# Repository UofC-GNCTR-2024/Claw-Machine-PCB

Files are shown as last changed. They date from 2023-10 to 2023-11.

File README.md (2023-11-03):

# Claw-Machine-PCB
PCB for the UofC GNCTR 2024 claw machine

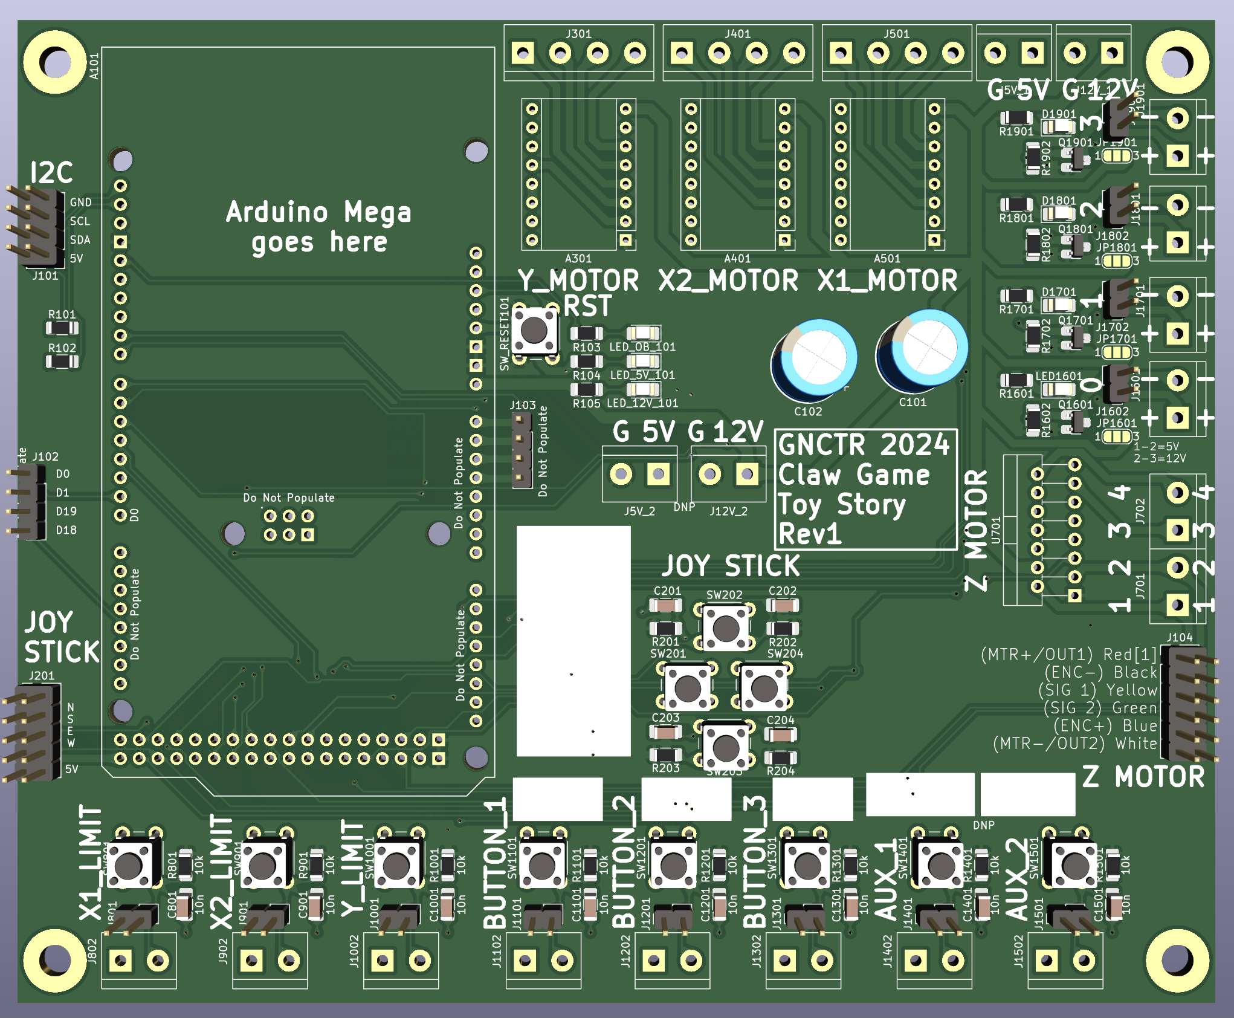
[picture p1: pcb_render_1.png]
PCB Render 1


## Main Components
1. 3x Stepper Motor Drivers
    * 2x will drive Y-axis, and 1x will drive X-axis
    * Model: A4988 Breakout
        * [Guide 1 - lastminuteengineers.com](https://lastminuteengineers.com/a4988-stepper-motor-driver-arduino-tutorial/)
    * The [microstep mode](https://lastminuteengineers.com/a4988-stepper-motor-driver-arduino-tutorial/#:~:text=power%20supply%20pins.-,Microstep%20Selection%20Pins,-The%20A4988%20driver) is locked in 1/16th Step Mode.
    * Add LEDs to each control signal
    * Signals (MCU to Driver, for each driver): STEP, DIR, EN

2. 1x DC Motor Driver
    * 1x for the claw to drop
    * Model: L298N (package: multiwatt vertical)
        * [Datasheet 1](https://www.sparkfun.com/datasheets/Robotics/L298_H_Bridge.pdf)
    * L298N contains 2x H-Bridges, so it can drive the 2x motors
    * Add LEDs to each control signal

3. Countdown Clock I2C Connector
    * Uses I2C (so only one bus)
    * Connection over 2.54mm headers

4. 10x Buttons and Limit Switches
    * 3x Limit Switches, 3x User Buttons, 2x Spare
    * Use 5.08mm screw terminal in parallel with 2.54mm header
    * Make them active-low, with external pull-up resistors
    * Put them in parallel with 6mm through-hole push buttons for validation

5. Control Stick
    * Model: [4-Way Switched Discrete Joystick](https://www.amazon.ca/Joystick-Classic-Competition-Arcade1up-Replacement/dp/B0BWWW8Z2J/ref=sr_1_15)
    * Basically 4x more buttons
    * Label them NESW, and use a common GND (5-pin 2.54mm header, but two of them side-by-side)

6. 1x Microcontroller System
    * Model: Arduino Mega 2560 clone
    * Footprint available via plugin

7. 4x General Power Output Channels
    * Use AO3420 MOSFETs, to be able to drive LEDs in the frame, etc.
    * Add a 3-way solder jumper to select between 5V or 12V power
    * Can be used fo LED strip lighting. One channel will be for the 12V claw solenoid.

8. Voltage Input Rails
    * 5V and 12V rails
    * Inputs via 5.08mm screw terminals
    * Powered from computer PSU

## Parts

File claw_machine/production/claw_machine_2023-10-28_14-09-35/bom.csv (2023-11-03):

Designator | Footprint | Quantity | Value | LCSC Part #
A101 | Arduino_Mega2560_R3_Shield | 1 | Arduino_Mega2560_R3_Shield
A301, A401, A501 | Pololu_Breakout-16_15.2x20.3mm | 3 | Pololu_Breakout_A4988
C1001, C1101, C1201, C1301, C1401, C1501, C201, C202, C203, C204, C801, C901 | 1206 | 12 | 10n
C101, C102 | CP_Radial_D10.0mm_P5.00mm_P7.50mm | 2 | 100u
D1701, D1801, D1901, LED1601, LED_12V_101, LED_5V_101, LED_OB_101 | 1206 | 7 | LED
H101, H102, H103, H104 | MountingHole_4.3mm_M4_Pad_TopBottom | 4 | MountingHole
J1001, J1101, J1201, J1301, J1401, J1501, J1602, J1702, J1802, J1902, J801, J901 | PinHeader_1x02_P2.54mm_Vertical | 12 | Conn_01x02
J1002, J1102, J1202, J12V_1, J1302, J1402, J1502, J1601, J1701, J1801, J1901, J5V_1, J701, J702, J802, J902 | TerminalBlock_bornier-2_P5.08mm | 16 | Screw_Terminal_01x02
J101 | PinHeader_2x04_P2.54mm_Vertical | 1 | ~
J102, J103 | PinHeader_1x04_P2.54mm_Vertical | 2 | Conn_01x04
J104 | PinHeader_2x06_P2.54mm_Vertical | 1 | Conn_02x06_Odd_Even
J201 | PinHeader_2x05_P2.54mm_Vertical | 1 | Conn_02x05_Odd_Even
J301, J401, J501 | TerminalBlock_bornier-4_P5.08mm | 3 | Screw_Terminal_01x04
JP1601, JP1701, JP1801, JP1901 | SolderJumper-3_P1.3mm_Open_RoundedPad1.0x1.5mm_NumberLabels | 4 | SolderJumper_3_Open
Q1601, Q1701, Q1801, Q1901 | SOT-23-MassivePads-HandSolder | 4 | AO3400A
R1001, R105, R1101, R1201, R1301, R1401, R1501, R1602, R1702, R1802, R1902, R201, R202, R203, R204, R801, R901 | 1206 | 17 | 10k
R101, R102 | 1206 | 2 | 3k3
R103, R104, R1601, R1701, R1801, R1901 | 1206 | 6 | 2k2
SW1001, SW1101, SW1201, SW1301, SW1401, SW1501, SW201, SW202, SW203, SW204, SW801, SW901, SW_RESET101 | SW_PUSH_6mm | 13 | SW_Push
U701 | TO-220-15_P2.54x2.54mm_StaggerOdd_Lead4.58mm_Vertical | 1 | L298N

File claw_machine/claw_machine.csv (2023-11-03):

Source: | /home/user/GitHub/Claw-Machine-PCB/claw_machine/claw_machine.kicad_sch
Date: | Fri 03 Nov 2023 04:45:17 PM
Tool: | Eeschema 7.0.8
Generator: | /app/share/kicad/plugins/bom_csv_grouped_by_value.py
Component Count: | 114
Collated Components:
Item | Qty | Reference(s) | Value | LibPart | Footprint | Datasheet | DNP
1 | 1 | A101 | Arduino_Mega2560_R3_Shield | PCM_arduino-library:Arduino_Mega2560_R3_Shield | PCM_arduino-library:Arduino_Mega2560_R3_Shield | https://docs.arduino.cc/hardware/mega-2560
2 | 3 | A301, A401, A501 | Pololu_Breakout_A4988 | Driver_Motor:Pololu_Breakout_A4988 | Module:Pololu_Breakout-16_15.2x20.3mm | https://www.pololu.com/product/2980/pictures
3 | 2 | C101, C102 | 100u | Device:C_Polarized | Capacitor_THT:CP_Radial_D10.0mm_P5.00mm_P7.50mm | ~
4 | 12 | C201, C202, C203, C204, C801, C901, C1001, C1101, C1201, C1301, C1401, C1501 | 10n | Device:C | Capacitor_SMD:C_1206_3216Metric_Pad1.33x1.80mm_HandSolder | ~
5 | 7 | D1701, D1801, D1901, LED1601, LED_5V_101, LED_12V_101, LED_OB_101 | LED | Device:LED | LED_SMD:LED_1206_3216Metric_Pad1.42x1.75mm_HandSolder | ~
6 | 4 | H101, H102, H103, H104 | MountingHole | Mechanical:MountingHole_Pad | MountingHole:MountingHole_4.3mm_M4_Pad_TopBottom | ~
7 | 16 | J5V_1, J12V_1, J701, J702, J802, J902, J1002, J1102, J1202, J1302, J1402, J1502, J1601, J1701, J1801, J1901 | Screw_Terminal_01x02 | Connector:Screw_Terminal_01x02 | TerminalBlock:TerminalBlock_bornier-2_P5.08mm | ~
8 | 2 | J5V_2, J12V_2 | Screw_Terminal_01x02 | Connector:Screw_Terminal_01x02 | TerminalBlock:TerminalBlock_bornier-2_P5.08mm | ~ | DNP
9 | 1 | J101 | ~ | Connector_Generic:Conn_02x04_Odd_Even | Connector_PinHeader_2.54mm:PinHeader_2x04_P2.54mm_Vertical | ~
10 | 2 | J102, J103 | Conn_01x04 | Connector_Generic:Conn_01x04 | Connector_PinHeader_2.54mm:PinHeader_1x04_P2.54mm_Vertical | ~
11 | 1 | J104 | Conn_02x06_Odd_Even | Connector_Generic:Conn_02x06_Odd_Even | Connector_PinHeader_2.54mm:PinHeader_2x06_P2.54mm_Vertical | ~
12 | 1 | J201 | Conn_02x05_Odd_Even | Connector_Generic:Conn_02x05_Odd_Even | Connector_PinHeader_2.54mm:PinHeader_2x05_P2.54mm_Vertical | ~
13 | 3 | J301, J401, J501 | Screw_Terminal_01x04 | Connector:Screw_Terminal_01x04 | TerminalBlock:TerminalBlock_bornier-4_P5.08mm | ~
14 | 12 | J801, J901, J1001, J1101, J1201, J1301, J1401, J1501, J1602, J1702, J1802, J1902 | Conn_01x02 | Connector_Generic:Conn_01x02 | Connector_PinHeader_2.54mm:PinHeader_1x02_P2.54mm_Vertical | ~
15 | 4 | JP1601, JP1701, JP1801, JP1901 | SolderJumper_3_Open | Jumper:SolderJumper_3_Open | Jumper:SolderJumper-3_P1.3mm_Open_RoundedPad1.0x1.5mm_NumberLabels | ~
16 | 4 | Q1601, Q1701, Q1801, Q1901 | AO3400A | Transistor_FET:AO3400A | Library:SOT-23-MassivePads-HandSolder | http://www.aosmd.com/pdfs/datasheet/AO3400A.pdf
17 | 2 | R101, R102 | 3k3 | Device:R | Resistor_SMD:R_1206_3216Metric_Pad1.30x1.75mm_HandSolder | ~
18 | 6 | R103, R104, R1601, R1701, R1801, R1901 | 2k2 | Device:R | Resistor_SMD:R_1206_3216Metric_Pad1.30x1.75mm_HandSolder | ~
19 | 17 | R105, R201, R202, R203, R204, R801, R901, R1001, R1101, R1201, R1301, R1401, R1501, R1602, R1702, R1802, R1902 | 10k | Device:R | Resistor_SMD:R_1206_3216Metric_Pad1.30x1.75mm_HandSolder | ~
20 | 13 | SW201, SW202, SW203, SW204, SW801, SW901, SW1001, SW1101, SW1201, SW1301, SW1401, SW1501, SW_RESET101 | SW_Push | Switch:SW_Push | Button_Switch_THT:SW_PUSH_6mm | ~
21 | 1 | U701 | L298N | Driver_Motor:L298N | Package_TO_SOT_THT:TO-220-15_P2.54x2.54mm_StaggerOdd_Lead4.58mm_Vertical | http://www.st.com/st-web-ui/static/active/en/resource/technical/document/datasheet/CD00000240.pdf

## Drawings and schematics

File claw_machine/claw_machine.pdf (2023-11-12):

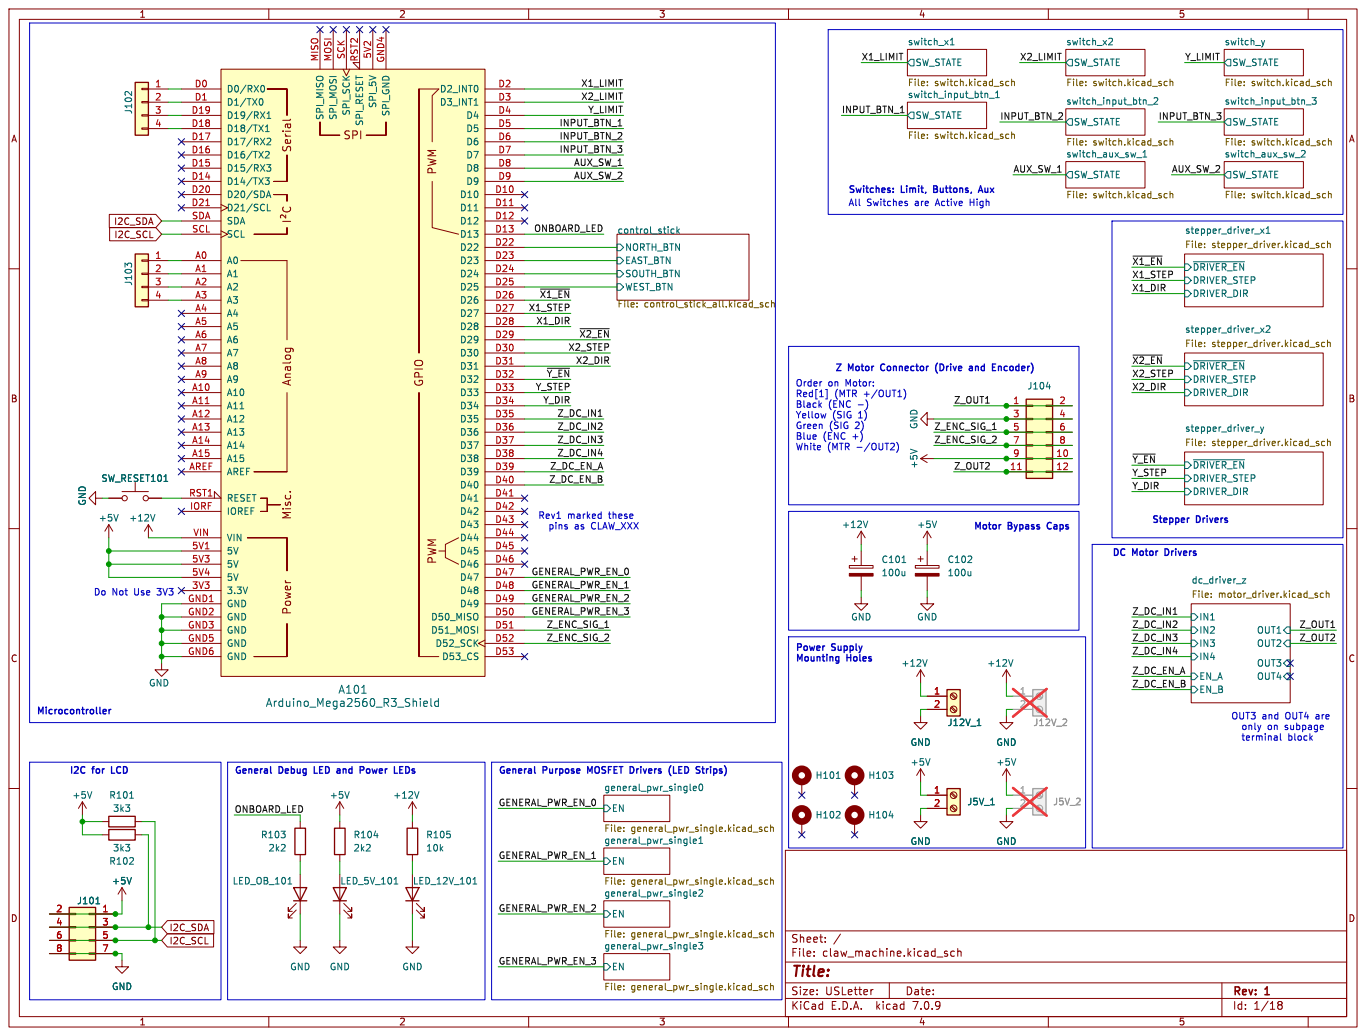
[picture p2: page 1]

SW_RESET101 GND
2 GND GND GND GND

Id: 1/18 Title: File: claw_machine.kicad_sch Sheet: /

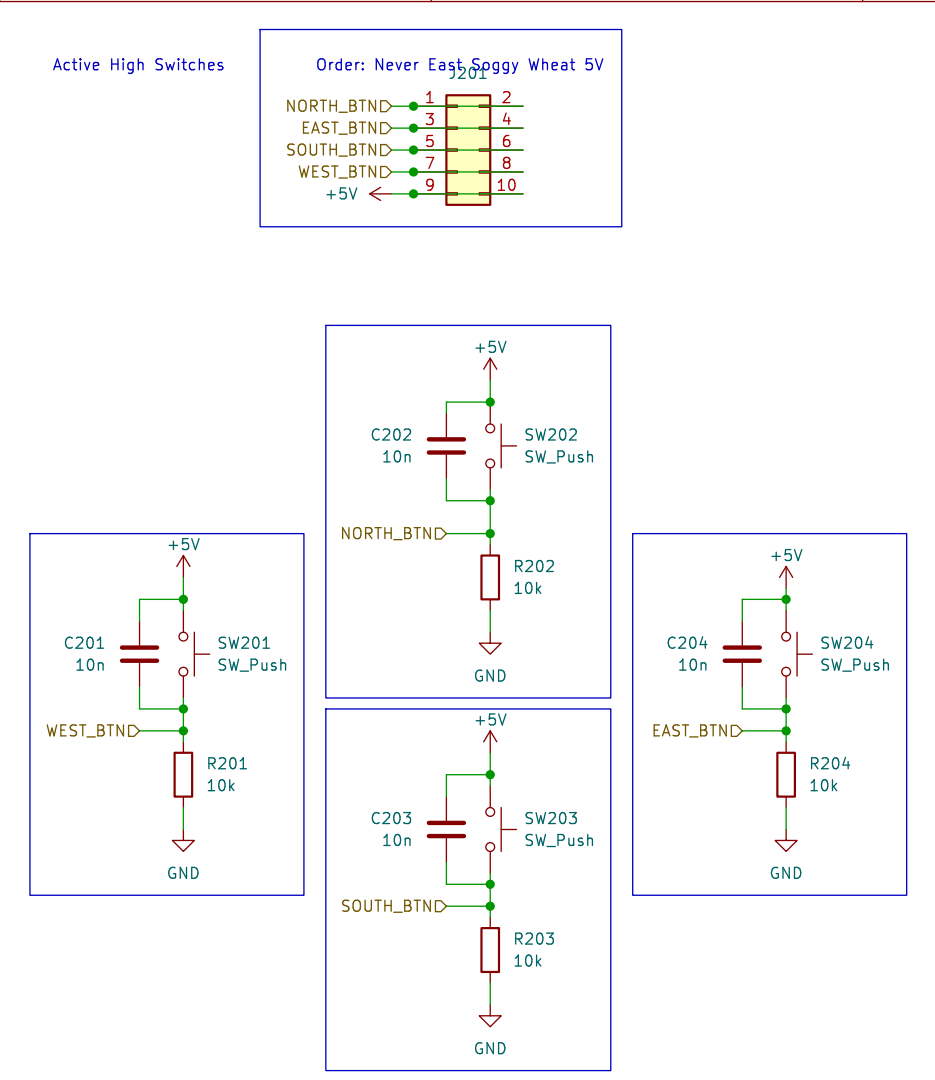
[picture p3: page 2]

Id: 2/18 Title: File: control_stick_all.kicad_sch Sheet: /control_stick/ R203

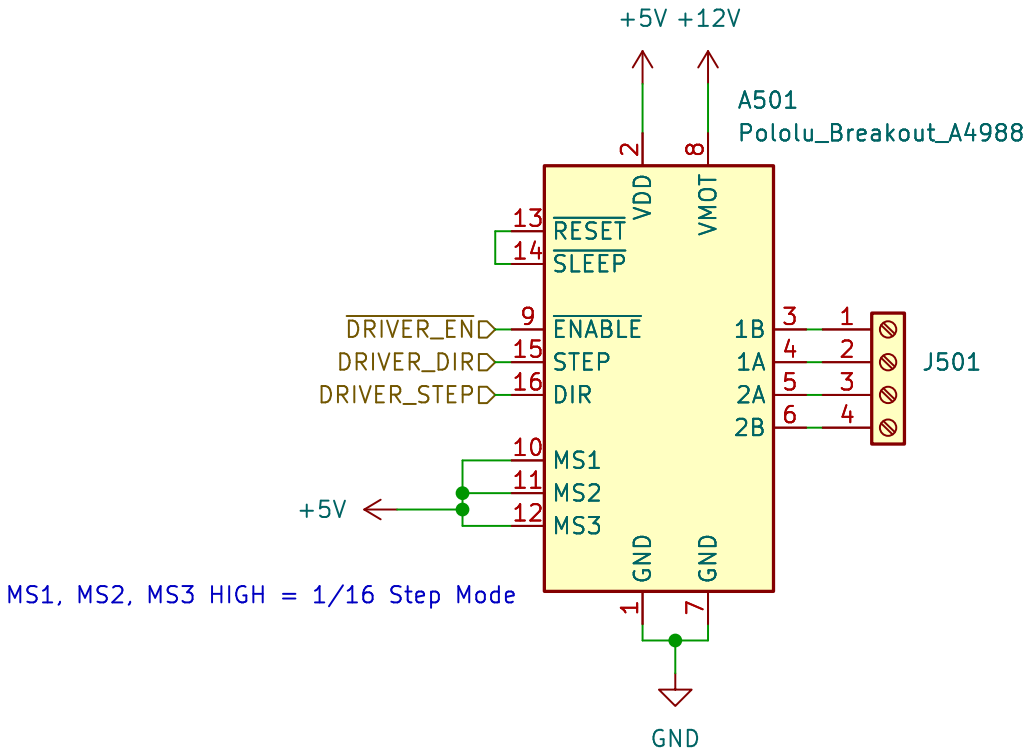
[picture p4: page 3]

1 MS1 10 MS2 11 MS3 12 ~{RESET} 13 ~{SLEEP} 14 STEP 15 DIR 16 VDD

Id: 4/18 Title: File: stepper_driver.kicad_sch Sheet: /stepper_driver_x1/

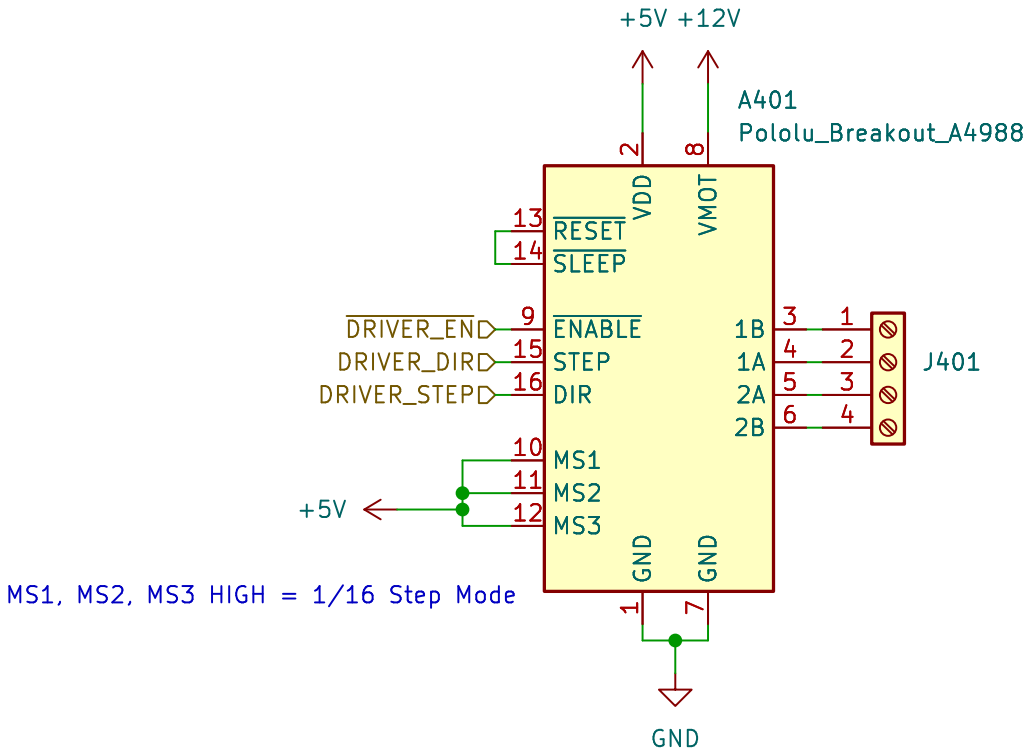
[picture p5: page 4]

1 MS1 10 MS2 11 MS3 12 ~{RESET} 13 ~{SLEEP} 14 STEP 15 DIR 16 VDD

Id: 5/18 Title: File: stepper_driver.kicad_sch Sheet: /stepper_driver_x2/

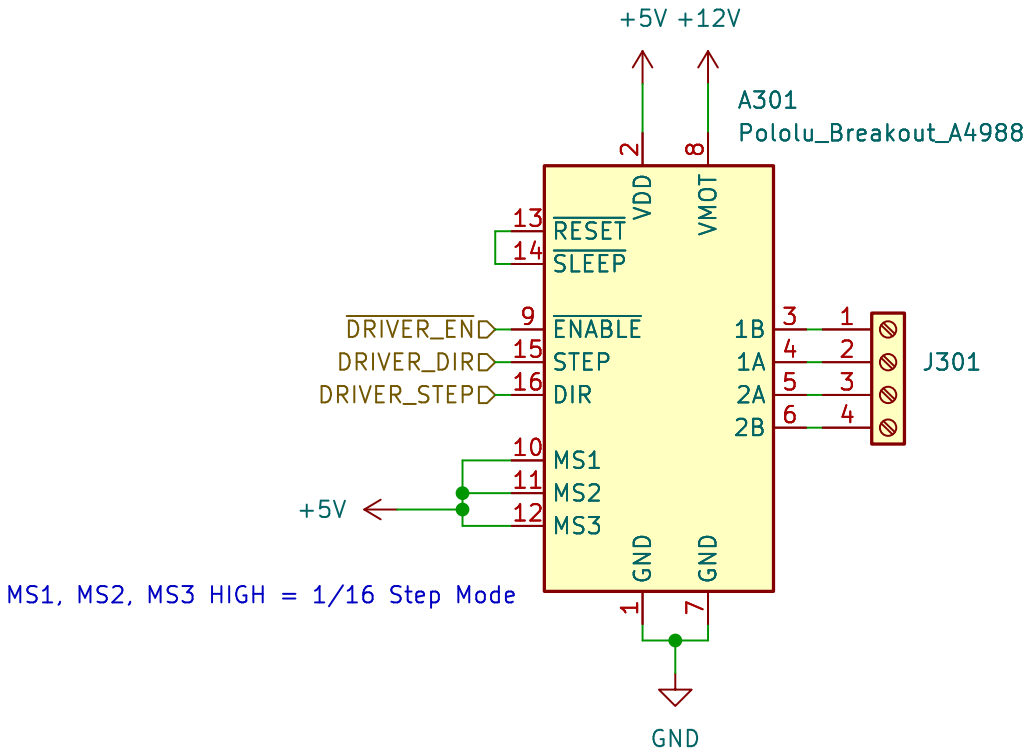
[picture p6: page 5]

1 MS1 10 MS2 11 MS3 12 ~{RESET} 13 ~{SLEEP} 14 STEP 15 DIR 16 VDD

Id: 6/18 Title: File: stepper_driver.kicad_sch Sheet: /stepper_driver_y/

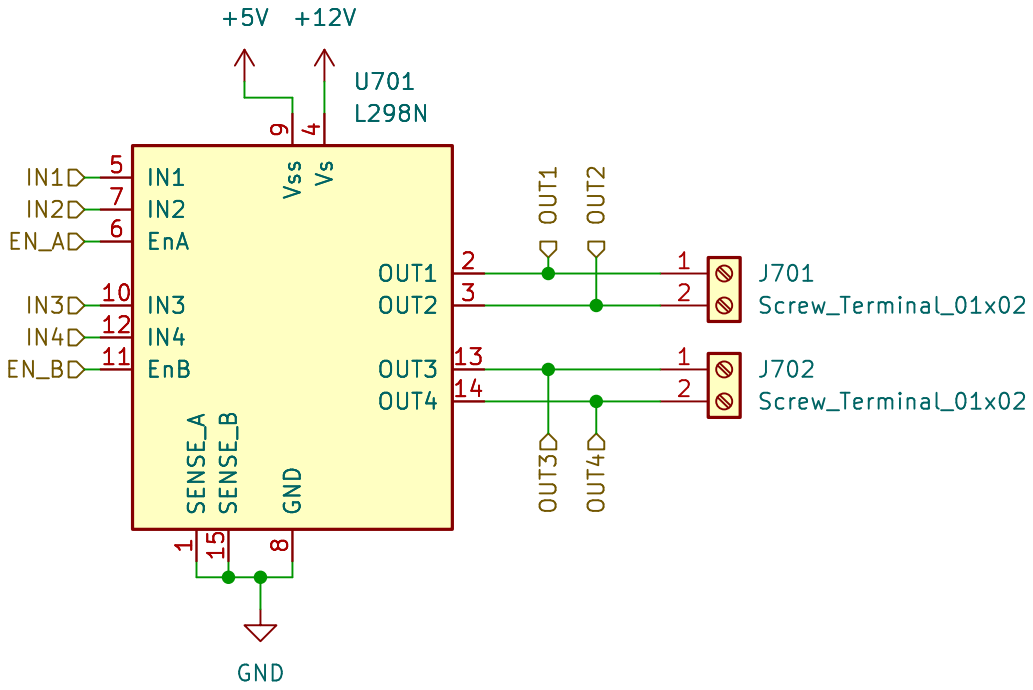
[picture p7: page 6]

Id: 8/18 Title: File: motor_driver.kicad_sch Sheet: /dc_driver_z/

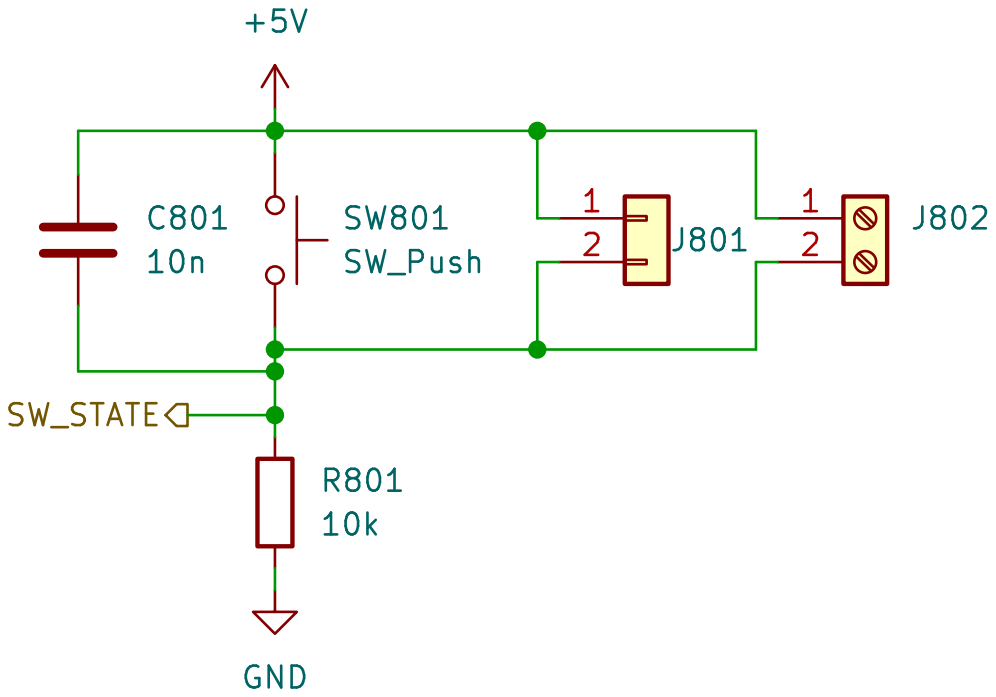
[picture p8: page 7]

Id: 9/18 Title: File: switch.kicad_sch Sheet: /switch_x1/

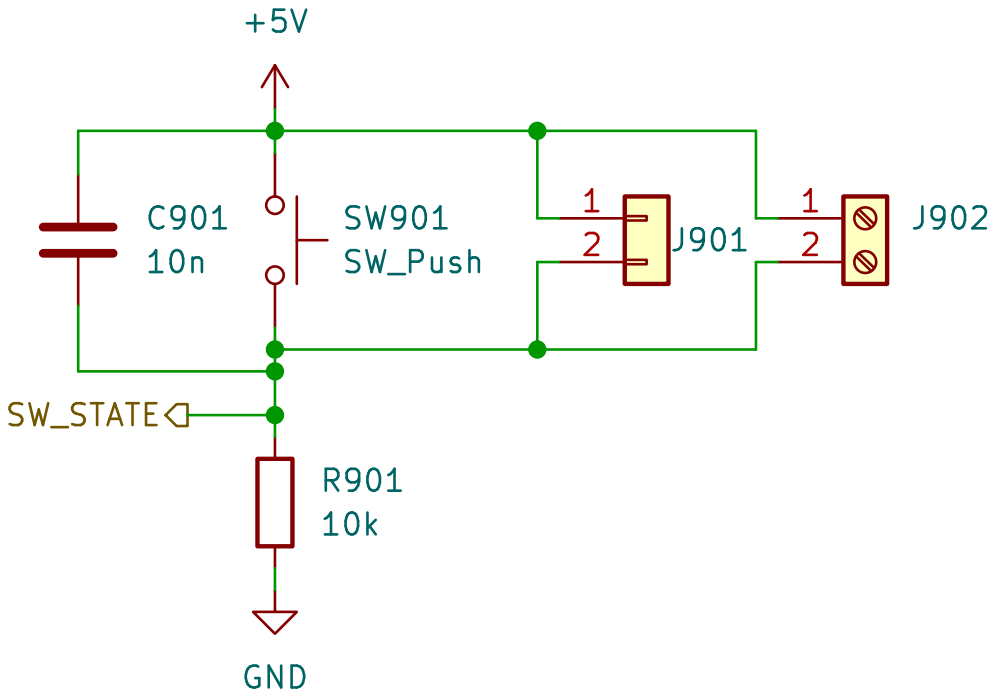
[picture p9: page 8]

Id: 10/18 Title: File: switch.kicad_sch Sheet: /switch_x2/

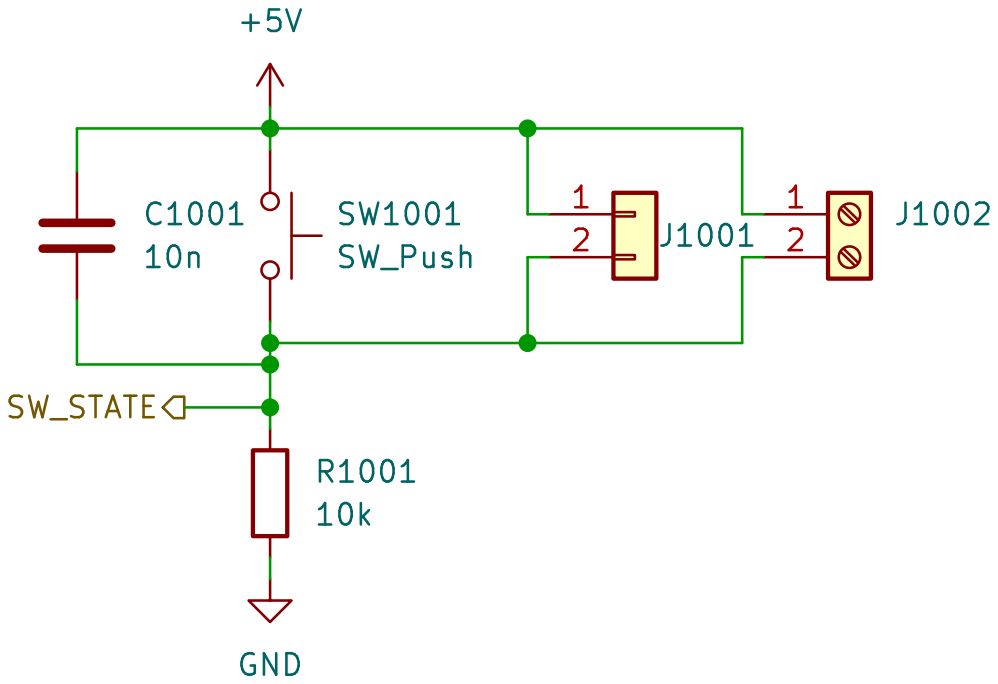
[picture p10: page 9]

Id: 11/18 Title: File: switch.kicad_sch Sheet: /switch_y/

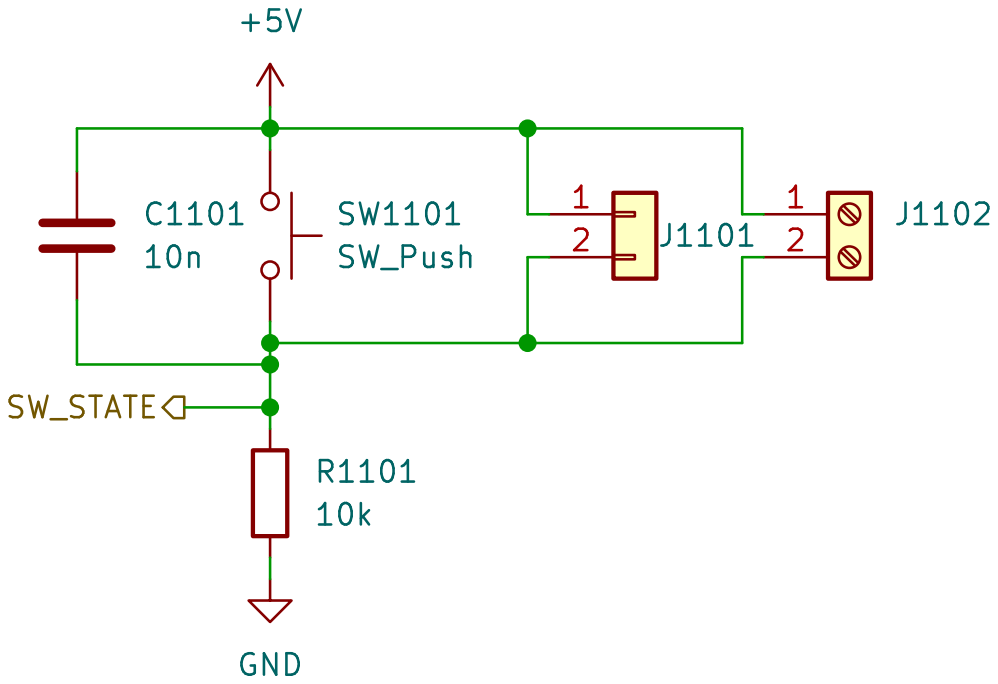
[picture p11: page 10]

Id: 12/18 Title: File: switch.kicad_sch Sheet: /switch_input_btn_1/

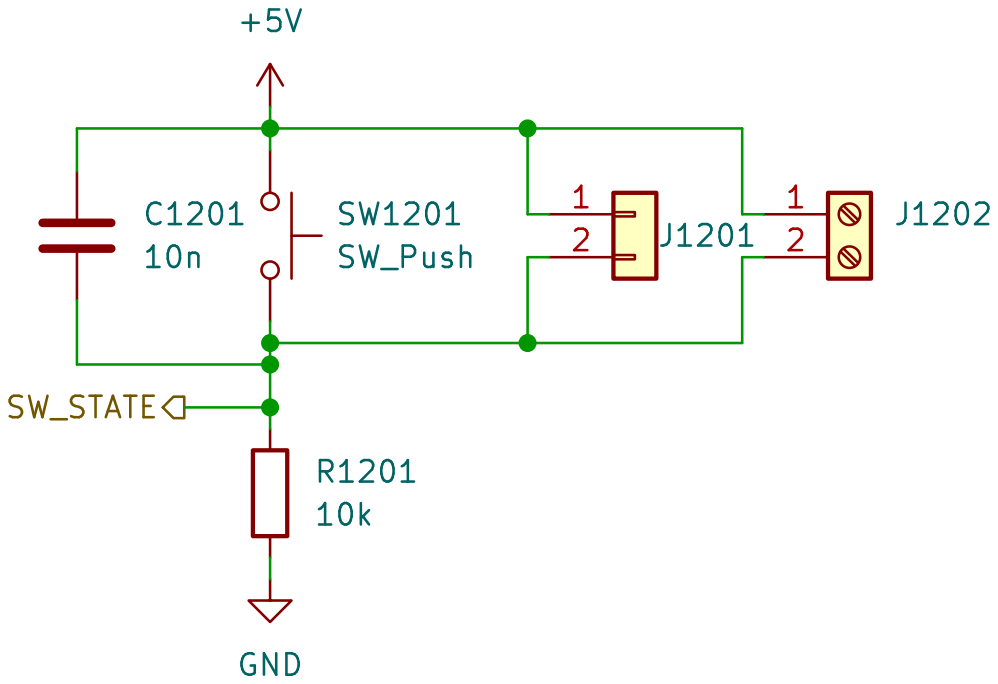
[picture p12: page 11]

Id: 13/18 Title: File: switch.kicad_sch Sheet: /switch_input_btn_2/

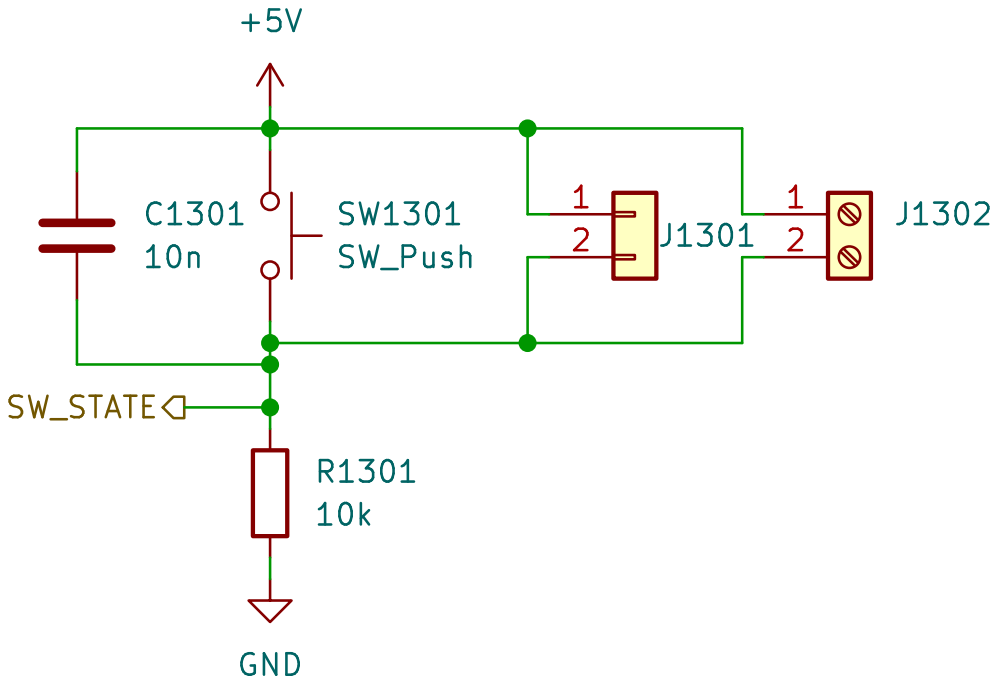
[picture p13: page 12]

Id: 14/18 Title: File: switch.kicad_sch Sheet: /switch_input_btn_3/


Id: 15/18 Title: File: switch.kicad_sch Sheet: /switch_aux_sw_1/


Id: 16/18 Title: File: switch.kicad_sch Sheet: /switch_aux_sw_2/


Id: 17/18 Title: File: general_pwr_single.kicad_sch Sheet: /general_pwr_single0/


Id: 18/18 Title: File: general_pwr_single.kicad_sch Sheet: /general_pwr_single1/


Id: 19/18 Title: File: general_pwr_single.kicad_sch Sheet: /general_pwr_single2/


Id: 20/18 Title: File: general_pwr_single.kicad_sch Sheet: /general_pwr_single3/

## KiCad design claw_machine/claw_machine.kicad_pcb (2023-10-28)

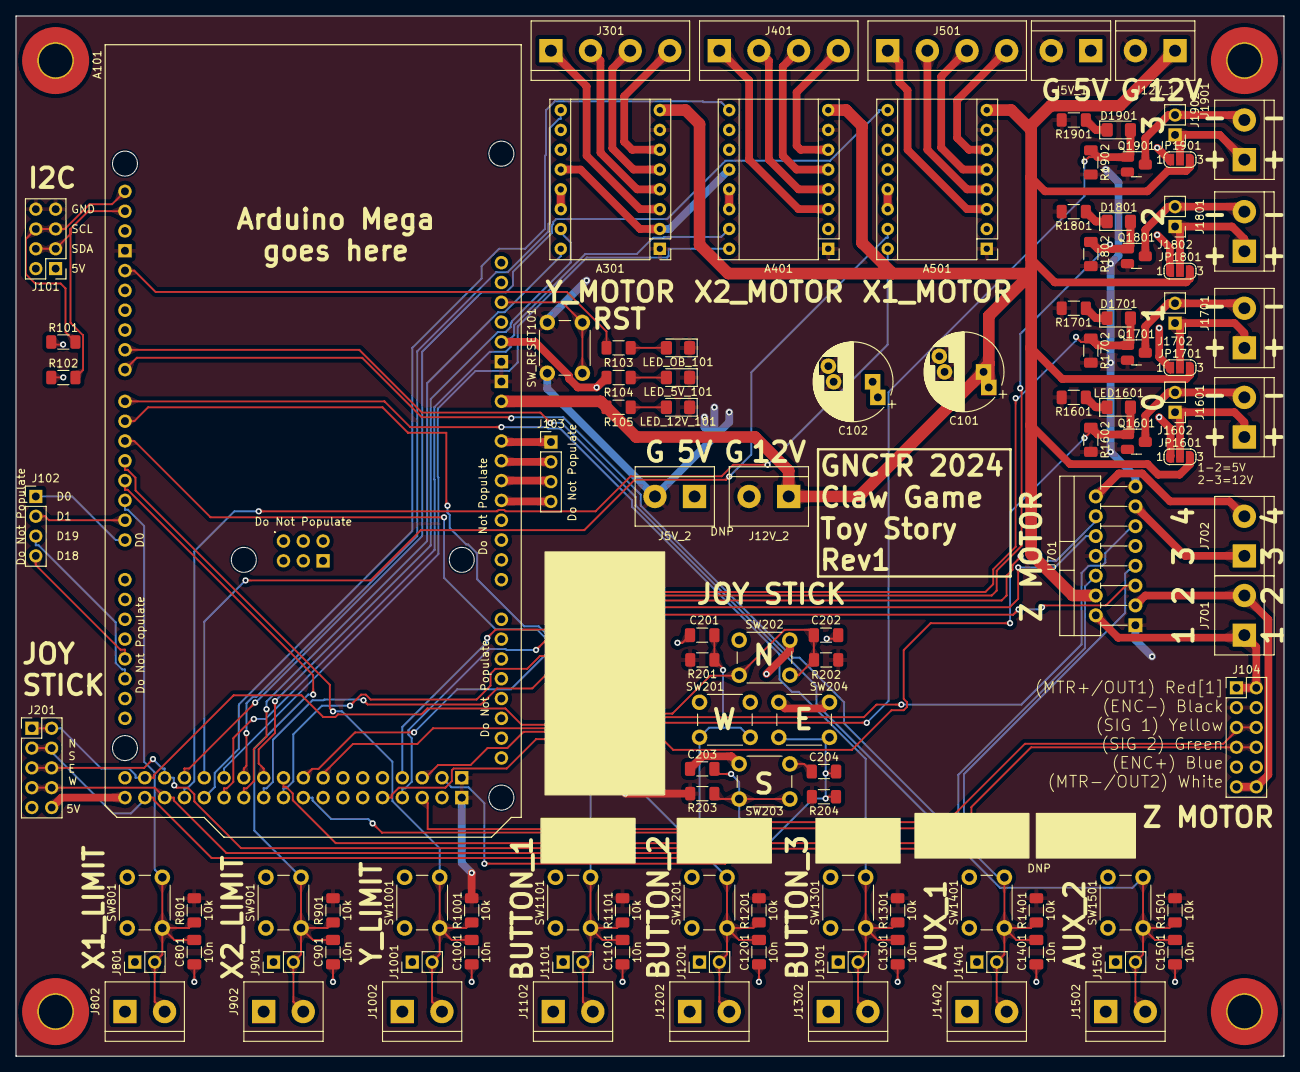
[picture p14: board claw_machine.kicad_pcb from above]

Board: 2 copper layers, 162.6 x 133.4 mm, 114 parts (1 on the bottom side), 82 nets.

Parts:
A101: Arduino_Mega2560_R3_Shield
A301, A401, A501: Pololu_Breakout_A4988; Pololu_Breakout-16_15.2x20.3mm
C101, C102: 100u; CP_Radial_D10.0mm_P5.00mm_P7.50mm
C201, C202, C203, C204, C801, C901, C1001, C1101, C1201, C1301, C1401, C1501: 10n; C_1206_3216Metric_Pad1.33x1.80mm_HandSolder
D1701, D1801, D1901: LED; LED_1206_3216Metric_Pad1.42x1.75mm_HandSolder
H101, H102, H103, H104: MountingHole; MountingHole_4.3mm_M4_Pad_TopBottom
J5V_1, J5V_2, J12V_1, J12V_2, J701, J702, J802, J902, J1002, J1102, J1202, J1302, J1402, J1502, J1601, J1701, J1801, J1901: Screw_Terminal_01x02; TerminalBlock_bornier-2_P5.08mm
J101: PinHeader_2x04_P2.54mm_Vertical
J102, J103: Conn_01x04; PinHeader_1x04_P2.54mm_Vertical
J104: Conn_02x06_Odd_Even; PinHeader_2x06_P2.54mm_Vertical
J201: Conn_02x05_Odd_Even; PinHeader_2x05_P2.54mm_Vertical
J301, J401, J501: Screw_Terminal_01x04; TerminalBlock_bornier-4_P5.08mm
J801, J901, J1001, J1101, J1201, J1301, J1401, J1501, J1602, J1702, J1802, J1902: Conn_01x02; PinHeader_1x02_P2.54mm_Vertical
JP1601, JP1701, JP1801, JP1901: SolderJumper_3_Open; SolderJumper-3_P1.3mm_Open_RoundedPad1.0x1.5mm_NumberLabels
LED1601: LED; LED_1206_3216Metric_Pad1.42x1.75mm_HandSolder
LED_5V_101, LED_12V_101: LED; LED_1206_3216Metric_Pad1.42x1.75mm_HandSolder
LED_OB_101: LED; LED_1206_3216Metric_Pad1.42x1.75mm_HandSolder
Q1601, Q1701, Q1801, Q1901: AO3400A; SOT-23-MassivePads-HandSolder
R101, R102: 3k3; R_1206_3216Metric_Pad1.30x1.75mm_HandSolder
R103, R104, R1601, R1701, R1801, R1901: 2k2; R_1206_3216Metric_Pad1.30x1.75mm_HandSolder
R105, R201, R202, R203, R204, R801, R901, R1001, R1101, R1201, R1301, R1401, R1501, R1602, R1702, R1802, R1902: 10k; R_1206_3216Metric_Pad1.30x1.75mm_HandSolder
SW201, SW202, SW203, SW204, SW801, SW901, SW1001, SW1101, SW1201, SW1301, SW1401, SW1501: SW_Push; SW_PUSH_6mm
SW_RESET101: SW_Push; SW_PUSH_6mm
U701: L298N; TO-220-15_P2.54x2.54mm_StaggerOdd_Lead4.58mm_Vertical

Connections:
+5V: A101.5V1 (5V), A101.5V3 (5V), A101.5V4 (5V), A301.2 (VDD), A301.10 (MS1), A301.11 (MS2), A301.12 (MS3), A401.2 (VDD), A401.10 (MS1), A401.11 (MS2), A401.12 (MS3), A501.2 (VDD), A501.10 (MS1), A501.11 (MS2), A501.12 (MS3), C102.1, C201.1, C202.1, C203.1, C204.1, C801.1, C901.1, C1001.1, C1101.1, C1201.1, C1301.1, C1401.1, C1501.1, J5V_1.1, J5V_2.1, J101.1, J101.2, J104.9, J104.10, J201.9, J201.10, J801.1, J802.1, J901.1, J902.1, J1001.1, J1002.1, J1101.1, J1102.1, J1201.1, J1202.1, J1301.1, J1302.1, J1401.1, J1402.1, J1501.1, J1502.1, JP1601.1 (A), JP1701.1 (A), JP1801.1 (A), JP1901.1 (A), R101.1, R102.1, R104.1, SW201.1, SW202.1, SW203.1, SW204.1, SW801.1, SW901.1, SW1001.1, SW1101.1, SW1201.1, SW1301.1, SW1401.1, SW1501.1, U701.9 (Vss)
+12V: A101.VIN, A301.8 (VMOT), A401.8 (VMOT), A501.8 (VMOT), C101.1, J12V_1.1, J12V_2.1, JP1601.3 (B), JP1701.3 (B), JP1801.3 (B), JP1901.3 (B), R105.1, U701.4 (Vs)
/AUX_SW_1: A101.D8, C1401.2, J1401.2, J1402.2, R1401.1, SW1401.2
/AUX_SW_2: A101.D9, C1501.2, J1501.2, J1502.2, R1501.1, SW1501.2
/GENERAL_PWR_EN_0: A101.D47, LED1601.2 (A), Q1601.1 (G), R1602.1
/GENERAL_PWR_EN_1: A101.D48, D1701.2 (A), Q1701.1 (G), R1702.1
/GENERAL_PWR_EN_2: A101.D49, D1801.2 (A), Q1801.1 (G), R1802.1
/GENERAL_PWR_EN_3: A101.D50 (D50_MISO), D1901.2 (A), Q1901.1 (G), R1902.1
/INPUT_BTN_1: A101.D5, C1101.2, J1101.2, J1102.2, R1101.1, SW1101.2
/INPUT_BTN_2: A101.D6, C1201.2, J1201.2, J1202.2, R1201.1, SW1201.2
/INPUT_BTN_3: A101.D7, C1301.2, J1301.2, J1302.2, R1301.1, SW1301.2
/ONBOARD_LED: A101.D13, R103.1
/X1_DIR: A101.D28, A501.15 (STEP)
/X1_LIMIT: A101.D2 (D2_INT0), C801.2, J801.2, J802.2, R801.1, SW801.2
/X1_STEP: A101.D27, A501.16 (DIR)
/X2_DIR: A101.D31, A401.15 (STEP)
/X2_LIMIT: A101.D3 (D3_INT1), C901.2, J901.2, J902.2, R901.1, SW901.2
/X2_STEP: A101.D30, A401.16 (DIR)
/Y_DIR: A101.D34, A301.15 (STEP)
/Y_LIMIT: A101.D4, C1001.2, J1001.2, J1002.2, R1001.1, SW1001.2
/Y_STEP: A101.D33, A301.16 (DIR)
/Z_DC_EN_A: A101.D39, U701.6 (EnA)
/Z_DC_EN_B: A101.D40, U701.11 (EnB)
/Z_DC_IN1: A101.D35, U701.5 (IN1)
/Z_DC_IN2: A101.D36, U701.7 (IN2)
/Z_DC_IN3: A101.D37, U701.10 (IN3)
/Z_DC_IN4: A101.D38, U701.12 (IN4)
/Z_ENC_SIG_1: A101.D51 (D51_MOSI), J104.5, J104.6
/Z_ENC_SIG_2: A101.D52 (D52_SCK), J104.7, J104.8
/Z_OUT1: J104.1, J104.2, J701.1, U701.2 (OUT1)
/Z_OUT2: J104.11, J104.12, J701.2, U701.3 (OUT2)
/control_stick/EAST_BTN: A101.D23, C204.2, J201.3, J201.4, R204.1, SW204.2
/control_stick/NORTH_BTN: A101.D22, C202.2, J201.1, J201.2, R202.1, SW202.2
/control_stick/SOUTH_BTN: A101.D24, C203.2, J201.5, J201.6, R203.1, SW203.2
/control_stick/WEST_BTN: A101.D25, C201.2, J201.7, J201.8, R201.1, SW201.2
/dc_driver_z/ OUT3: J702.1, U701.13 (OUT3)
/dc_driver_z/ OUT4: J702.2, U701.14 (OUT4)
/~X1_EN: A101.D26, A501.9 (~ENABLE)
/~X2_EN: A101.D29, A401.9 (~ENABLE)
/~Y_EN: A101.D32, A301.9 (~ENABLE)
GND: A101.GND1 (GND), A101.GND2 (GND), A101.GND3 (GND), A101.GND5 (GND), A101.GND6 (GND), A301.1 (GND), A301.7 (GND), A401.1 (GND), A401.7 (GND), A501.1 (GND), A501.7 (GND), C101.2, C102.2, J5V_1.2, J5V_2.2, J12V_1.2, J12V_2.2, J101.7, J101.8, J104.3, J104.4, LED_5V_101.1 (K), LED_12V_101.1 (K), LED_OB_101.1 (K), Q1601.2 (S), Q1701.2 (S), Q1801.2 (S), Q1901.2 (S), R201.2, R202.2, R203.2, R204.2, R801.2, R901.2, R1001.2, R1101.2, R1201.2, R1301.2, R1401.2, R1501.2, R1601.2, R1602.2, R1701.2, R1702.2, R1801.2, R1802.2, R1901.2, R1902.2, SW_RESET101.1, U701.1 (SENSE_A), U701.8 (GND), U701.15 (SENSE_B)
I2C_SCL: A101.SCL, J101.5, J101.6, R101.2
I2C_SDA: A101.SDA, J101.3, J101.4, R102.2
unnamed: A101.D0 (D0/RX0), J102.1
unnamed: A101.D1 (D1/TX0), J102.2
unnamed: A101.D18 (D18/TX1), J102.4
unnamed: A101.D19 (D19/RX1), J102.3
unnamed: A101.RST1 (RESET), SW_RESET101.2
unnamed: A301.4 (1A), J301.2
unnamed: A301.3 (1B), J301.1
unnamed: A301.5 (2A), J301.3
unnamed: A301.6 (2B), J301.4
unnamed: A301.13 (~RESET), A301.14 (~SLEEP)
unnamed: A401.4 (1A), J401.2
unnamed: A401.3 (1B), J401.1
unnamed: A401.5 (2A), J401.3
unnamed: A401.6 (2B), J401.4
unnamed: A401.13 (~RESET), A401.14 (~SLEEP)
unnamed: A501.4 (1A), J501.2
unnamed: A501.3 (1B), J501.1
unnamed: A501.5 (2A), J501.3
unnamed: A501.6 (2B), J501.4
unnamed: A501.13 (~RESET), A501.14 (~SLEEP)
unnamed: D1701.1 (K), R1701.1
unnamed: D1801.1 (K), R1801.1
unnamed: D1901.1 (K), R1901.1
unnamed: A101.A0, J103.1
unnamed: A101.A1, J103.2
unnamed: A101.A2, J103.3
unnamed: A101.A3, J103.4
unnamed: J1601.1, J1602.1, JP1601.2 (C)
unnamed: J1601.2, J1602.2, Q1601.3 (D)
unnamed: J1701.1, J1702.1, JP1701.2 (C)
unnamed: J1701.2, J1702.2, Q1701.3 (D)
unnamed: J1801.1, J1802.1, JP1801.2 (C)
unnamed: J1801.2, J1802.2, Q1801.3 (D)
unnamed: J1901.1, J1902.1, JP1901.2 (C)
unnamed: J1901.2, J1902.2, Q1901.3 (D)
unnamed: LED1601.1 (K), R1601.1
unnamed: LED_5V_101.2 (A), R104.2
unnamed: LED_12V_101.2 (A), R105.2
unnamed: LED_OB_101.2 (A), R103.2

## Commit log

2023-10-21 make more modular
    [ClawMachine.kicad_sch, control_stick.kicad_sch, control_stick_all.kicad_sch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]
2023-10-23 add clk, drivers & pwr
    [ClawMachine.kicad_sch, countdown_clk.kicad_sch, dc_driver_all.kicad_sch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]
2023-10-23 add pcb? i think
    [ClawMachine.kicad_pcb]
2023-10-23 change folder stuff & update gen pwr
    [ClawMachine.kicad_pcb, claw_machine.kicad_pcb, claw_machine.kicad_sch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]
2023-10-23 update limit switches to active high
    [limit_switches.kicad_sch]
2023-10-27 Rework schematic
    [claw_machine.kicad_pcb, claw_machine.kicad_sch, control_stick_all.kicad_sch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]
2023-10-27 Remove deleted sheets
    [control_stick.kicad_sch, countdown_clk.kicad_sch, dc_driver_all.kicad_sch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]
2023-10-27 Assign footprints
    [claw_machine.kicad_sch, control_stick_all.kicad_sch, general_pwr_single.kicad_sch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]
2023-10-27 Tiny bit of PCB work
    [claw_machine.kicad_sch, control_stick_all.kicad_sch, switch.kicad_sch]
2023-10-27 Start PCB work
    [claw_machine.kicad_pcb]
2023-10-27 Do most of the PCB layout
    [claw_machine.kicad_pcb, claw_machine.kicad_sch, control_stick_all.kicad_sch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]
2023-10-27 Route all power traced and replicated sections
    [claw_machine.kicad_pcb, general_pwr_single.kicad_sch, motor_driver.kicad_sch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]
2023-10-27 Minor change reconcile
    [claw_machine.kicad_pcb, general_pwr_single.kicad_sch, switch.kicad_sch]
2023-10-28 Autoroute and clean up manually
    [claw_machine.kicad_pcb]
2023-10-28 Add teardrops
    [claw_machine.kicad_pcb]
2023-10-28 Add names
    [claw_machine.kicad_pcb]
2023-10-28 Finish, Gerbers
    [claw_machine.kicad_pcb, claw_machine.kicad_sch, motor_driver.kicad_sch]
2023-11-03 Lock in rev1 production products, docs
    [bom.csv, claw_machine.csv, designators.csv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]
2023-11-09 Rename rev1 production files
    [bom.csv, designators.csv, positions.csv]
2023-11-12 Update schematic text, remove unused nets for CLAW motor
    [claw_machine.kicad_sch, control_stick_all.kicad_sch, general_pwr_single.kicad_sch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]
